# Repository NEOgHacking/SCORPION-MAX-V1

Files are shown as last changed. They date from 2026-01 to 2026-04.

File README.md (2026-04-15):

# 3D printer / CNC Mainboard
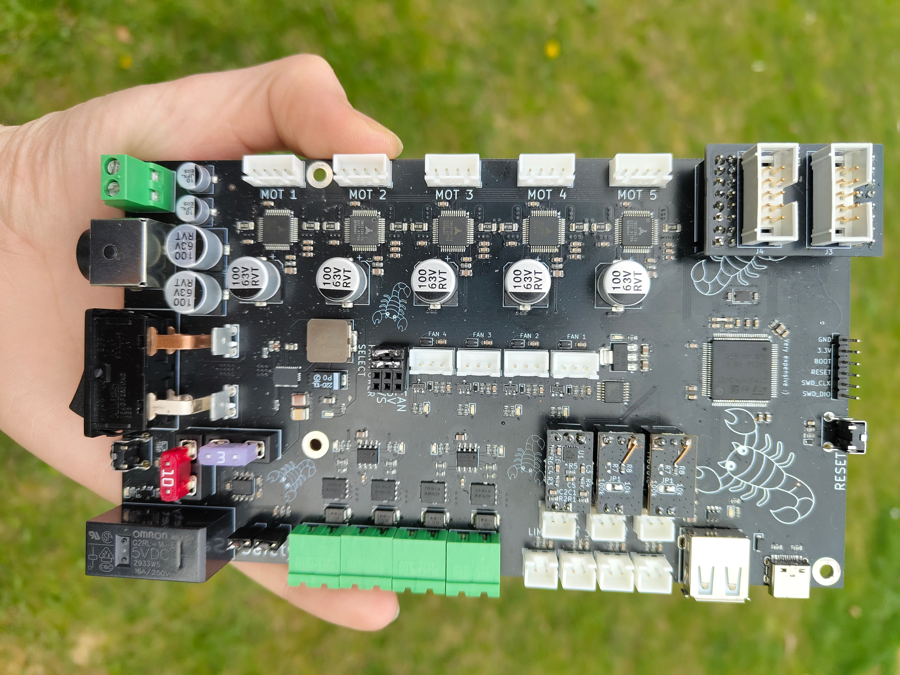
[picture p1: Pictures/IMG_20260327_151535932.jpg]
PCB SCORPION MAX V1

PCB SCORPION MAX V1
A main board for a 3d printer or CNC with wide possibilities with the use of the expansion board and thermistor boards! This board is based on the STM32H743 for its massive power. And everyone hates loud stepper motors, so it uses the TMC2130 silent stepper drivers, these are not only very quiet but have a lot of other functions!

# Video of working
Watch the video (https://youtube.com/shorts/JvQLqBAzKsY?feature=share)
# Reason
So long story longer I have an ultimaker 2+ laying at home doing nothing because of the noisy stepper drivers and recently getting an ultimaker S5 so I wanted to make it quieter and more useful. I was amazed by the Prusa mini being so quiet, so I thought why not build my own mainboard with way more quiet stepper drivers and more functions. The second reason is that I am planning to build a CNC somewhere in the future so I thought it would be a genius idea to build my own 3D printer / CNC mainboard with my own overkill specs and the best stepper drivers. And most of all A LOT of power in amps and compute!

# Specs
5x Stepper driver TMC2130

4x Power Mosfets for controlling heated beds, heaters, ext.

4x Fan controller with tacho input

4x Limit switches for homing

3x Thermistor inputs with possibilities for NTC's and PTC's
  These possibilities are possible because of the 2 thermistor boards I have designed, and the NTC thermistor board has a solder jumper to select the resistance of you NTC.

2x Safety inputs for disabling cutting power via a relay to the stepper drivers and mosfets

Expansion port for displays, SD cards, ext.

STM32H743VIT6 for big storage and calculation power

Standard 4 pin power connector and 2 pin screw terminal

USB ports, USB-C for programming and external control and USB-A for USB flash drives

# Design
This board is designed with a lot of safety features and well thought out design, it has a safety circuit to cut power to the steppers and heaters, good pcb design, followed design recommendation from datasheets, used the right components, and allot more! The pcb has been designed with the right trace width and good trace layout with no sharp bends. Also have good pcb layout.
# Schematics
There are 3 schematics for this project:
1. Main board
2. Thermistor modules
3. Expansion module

These are way too long to display here (14 pages) so in the PCB folder there in folder for the board you want to see there is a pdf file of the schematic, but here are a few.
Printer Mainboard page 1
Printer Mainboard page 9
Printer Mainboard page 10
Expansion board
PTC
NTC

# PCB

Main board




Thermistor boards




Expansion board




# Panalization
I have panelized the thermistor boards for better price per board, the panel still is under the 100x100 limit for the 2 dollar offer on jlcpcb so it’s still very cheap. I needed 6 thermistors for 2 boards and minimum order quantity on jlcpcb is 5, so I made a panel.



# Firmware
The firmware provided is Marlin, but I plan to expand this to more firmware’s like Clipper ext. The board is based on the STM32H743 so it's very powerful and can run almost any firmware!

# BOM
I have made a BOM for LCSC and a global BOM for all the parts and PCBs these are in the BOM folder
The price of the LCSC BOM for all the parts is about 180 dollars for 2 boards and the JLCPCB order is at the 54 dollar.
This is not the cheapest board but it does have the most functions!

# Credits
@Kai Pereira for all my random questions regarding PCB design and blueprint custom project. and for telling me long journals are the best, sorry for the short ones at the beginning. whoops.
Henk, someone I know that is way better in PCB design than me that looked over my schematic and layout ext.

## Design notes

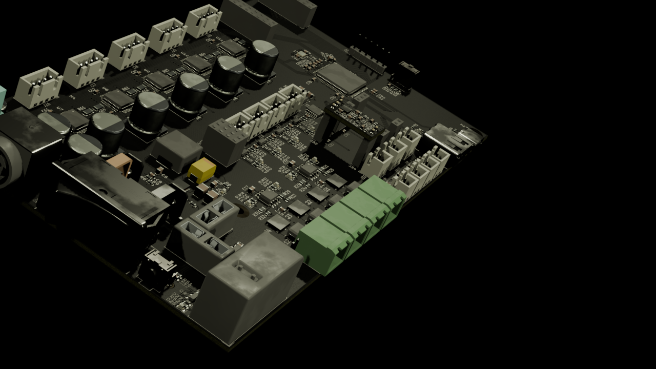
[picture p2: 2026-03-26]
Pictures/Renders/Render SCORPION MAX V1.png0072.png

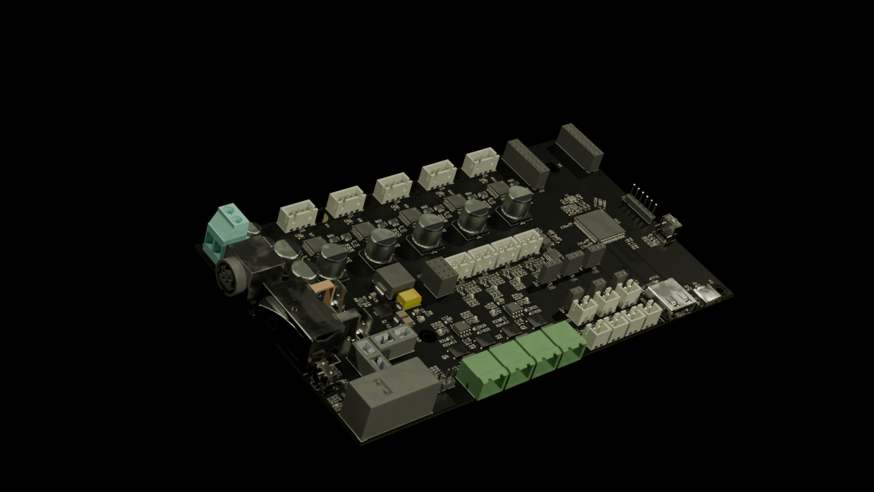
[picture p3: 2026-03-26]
Pictures/Renders/Render SCORPION MAX V1.png0001.png

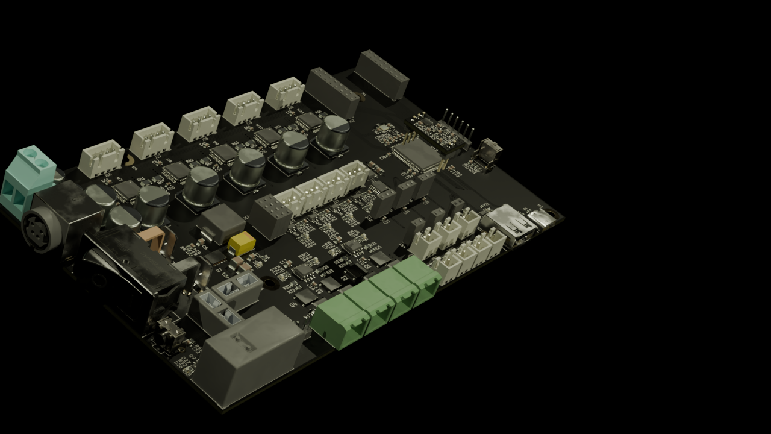
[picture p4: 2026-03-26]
Pictures/Renders/Render SCORPION MAX V1.png0026.png

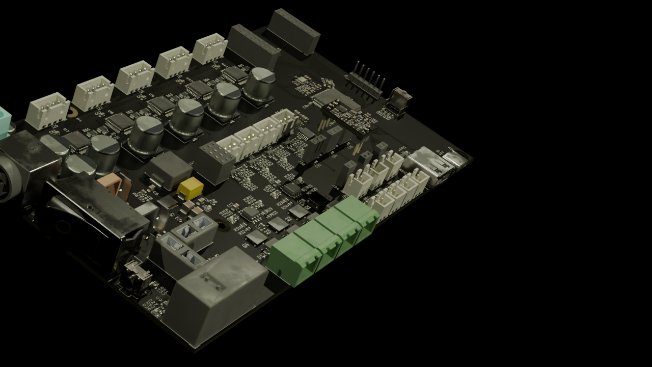
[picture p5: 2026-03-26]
Pictures/Renders/Render SCORPION MAX V1.png0035.png

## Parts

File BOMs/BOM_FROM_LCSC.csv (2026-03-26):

SCORPION MAX V1 |  |  |  |  |  |  |  |  |  | LCSC BOM Quotation
 |  |  |  |  |  |  |  |  |  | BOM Date Created：11/01/26 03:50:32 |  |  |  | BOM Export Date: 12/01/26 06:11:32 |  |  |  | The matching result is a real-time query result, availability and prices may fluctuate. Backorder items are estimated prices for your reference, please submit "Create Quote" to get the real price. All information is provided "as is" and is subject to change without notice. Any use made of the information provided is without recourse to LCSC and at the user's risk.
 |  |  |  |  |  |  |  |  |  | EST TOTAL :$156.41 |  |  |  | Website：https://www.lcsc.com/bom
Uploaded data |  |  |  |  |  |  |  |  |  | LCSC Matching Results
LCSC# | Mfr. | Mrf# | Description | Package | Value | Customer Part Number | Quantity | Target Price(EUR) | Target Lead Time(Business Days) | Mrf# | Mfr. | Order Qty. | Unit Price(EUR) | Ext.Price(EUR) | LCSC# | Package | Min | Mult | SPQ | Availability | Stock Status | Customer Notes | Description | Matched status | Product Link
 |  |  |  |  |  | 28 | 5 |  |  | TYPE-C-31-M-12 | Korean Hroparts Elec | 5 | 0.1553 | 0.78 | C165948 | SMD | 5 | 5 | 1000 | 428540 | In Stock |  | USB-C (USB TYPE-C) Receptacle Connector 16 Position Surface Mount | Exact Matches | https://www.lcsc.com/product-detail/C165948.html
 |  |  |  |  |  | 19 | 10 |  |  | SMBJ64A | R+O | 10 | 0.0441 | 0.44 | C19077594 | DO-214AA(SMB) | 10 | 10 | 3000 | 70550 | In Stock |  | 103VC Clamp 5.83A@10/1000us Ipp TVS DIODE DO-214AA(SMB) | Exact Matches | https://www.lcsc.com/product-detail/C19077594.html
 |  |  |  |  |  | 22 | 50 |  |  | 1N5819WS | Guangdong Hottech | 50 | 0.0083 | 0.42 | C191023 | SOD-323 | 50 | 50 | 3000 | 2274200 | In Stock |  | Diode 40V 1A Surface Mount SOD-323 | Exact Matches | https://www.lcsc.com/product-detail/C191023.html
 |  |  |  |  |  | 23 | 100 |  |  | 1N4148WT | JSMSEMI | 100 | 0.0050 | 0.50 | C917006 | SOD-523 | 100 | 100 | 3000 | 942700 | In Stock |  | Diode Independent 75V 150mA Surface Mount SOD-523 | Exact Matches | https://www.lcsc.com/product-detail/C917006.html
 |  |  |  |  |  | 24 | 10 |  |  | BAT54KFILM | ST | 10 | 0.0684 | 0.68 | C283259 | SOD-523 | 10 | 10 | 3000 | 2120 | In Stock |  | Diode 40V 300mA Surface Mount SOD-523 | Exact Matches | https://www.lcsc.com/product-detail/C283259.html
 |  |  |  |  |  | 43 | 2 |  |  | IHLP4040DZER6R8M01 | VISHAY | 2 | 0.8322 | 1.66 | C845080 | SMD,10.8x10.2mm | 1 | 1 | 500 | 48 | In Stock |  | 8A 6.8uH ±20% 23.3mΩ 13.5A SMD,10.8x10.2mm Fixed Inductors RoHS | Exact Matches | https://www.lcsc.com/product-detail/C845080.html
 |  |  |  |  |  | 27 | 2 |  |  | USB-302-T | SOFNG | 2 | 0.1055 | 0.21 | C112456 | Through Hole,Right Angle | 1 | 1 | 100 | 7704 | In Stock |  | USB-A (USB TYPE-A) Receptacle Connector 4 Position Right Angle | Exact Matches | https://www.lcsc.com/product-detail/C112456.html
 |  |  |  |  |  | 71 | 5 |  |  | NE555DR | TI | 5 | 0.0852 | 0.43 | C7593 | SOIC-8 | 5 | 5 | 2500 | 115150 | In Stock |  | SOIC-8 Programmable Timers and Oscillators RoHS | Exact Matches | https://www.lcsc.com/product-detail/C7593.html
 |  |  |  |  |  | 64 | 5 |  |  | STMPS2141STR | ST | 5 | 0.2987 | 1.49 | C54624 | SOT-23-5 | 5 | 5 | 3000 | 2220 | In Stock |  | SOT-23-5 Power Distribution Switches, Load Drivers RoHS | Exact Matches | https://www.lcsc.com/product-detail/C54624.html
 |  |  |  |  |  | 72 | 10 |  |  | TMC2130-TA-T | TRINAMIC | 10 | 4.3494 | 43.49 | C328952 | TQFP-48-EP(7x7) | 1 | 1 | 2000 | 1640 | In Stock |  | TQFP-48-EP(7x7) Motor Drivers, Controllers RoHS | Exact Matches | https://www.lcsc.com/product-detail/C328952.html
 |  |  |  |  |  | 68 | 5 |  |  | AP7361C-33E-13 | DIODES | 5 | 0.2142 | 1.07 | C500795 | SOT-223 | 5 | 5 | 2500 | 250 | In Stock |  | 6V Positive Fixed 3.3V SOT-223 Voltage Regulators - Linear, Low Drop Out (LDO) Regulators RoHS | Exact Matches | https://www.lcsc.com/product-detail/C500795.html
 |  |  |  |  |  | 67 | 5 |  |  | USBLC6-2SC6 | ST | 5 | 0.1155 | 0.58 | C7519 | SOT-23-6L | 5 | 5 | 3000 | 9985 | In Stock |  | 17VC Clamp 5A Ipp ESD DIODE SOT-23-6L | Exact Matches | https://www.lcsc.com/product-detail/C7519.html
 |  |  |  |  |  | 74 | 5 |  |  | NX3225GA-25.000M-STD-CRG-2 | NDK | 5 | 0.2464 | 1.23 | C1985619 | SMD3225-4P | 5 | 5 | 3000 | 1600 | In Stock |  | Crystal 25MHz ±20ppm 8pF 50Ω SMD3225-4P | Exact Matches | https://www.lcsc.com/product-detail/C1985619.html
 |  |  |  |  |  | 44 | 10 |  |  | NVMFWS4D5N08XT1G | onsemi | 10 | 1.5580 | 15.58 | C29841638 | DFNW-5(5x6) | 1 | 1 | 1500 | 48 | In Stock |  | 80V 92A 3.6V 4.5mΩ@10V 1 N-channel 82W DFNW-5(5x6) Single FETs, MOSFETs RoHS | Exact Matches | https://www.lcsc.com/product-detail/C29841638.html
 |  |  |  |  |  | 66 | 5 |  |  | B3F-3120 | OMRON | 5 | 0.1885 | 0.94 | C231318 | Through Hole | 5 | 5 | 1000 | 2070 | In Stock |  | Tactile Switch SPST 100gf 1.6mm PC Pin Through Hole, Right Angle | Exact Matches | https://www.lcsc.com/product-detail/C231318.html
 |  |  |  |  |  | 34 | 10 |  |  | 63849-1 | TE Connectivity | 10 | 0.0578 | 0.58 | C86469 | Through Hole | 10 | 10 | 2000 | 11260 | In Stock |  | Through Hole Quick Connects, Quick Disconnect Connectors RoHS | Exact Matches | https://www.lcsc.com/product-detail/C86469.html
 |  |  |  |  |  | 36 | 2 |  |  | 1711725 | Phoenix Contact | 2 | 0.9011 | 1.80 | C89120 | Through Hole,P=5.08mm | 1 | 1 | 100 | 893 | In Stock |  | 2 Position Wire to Board Terminal Block Through Hole 5.08mm | Exact Matches | https://www.lcsc.com/product-detail/C89120.html
 |  |  |  |  |  | 302 | 5 |  |  | SS11-BBIWG-R20-R | Legion | 5 | 0.2283 | 1.14 | C309069 | Through Hole,21x15mm | 5 | 5 | 500 | 2870 | In Stock |  | Rocker Switch SPST 16A(AC) 250V Through Hole | Exact Matches | https://www.lcsc.com/product-detail/C309069.html
 |  |  |  |  |  | 25 | 5 |  |  | XF-508P-B-B | XFCN | 5 | 0.2015 | 1.01 | C19727305 | DIP-4 | 5 | 5 | 500 | 28605 | In Stock |  | Blade 15A Clip 1 DIP-4 Fuseholders RoHS | Exact Matches | https://www.lcsc.com/product-detail/C19727305.html
 |  |  |  |  |  | 301 | 10 |  |  | 1757019 | Phoenix Contact | 10 | 0.6432 | 6.43 | C90073 | P=5.08mm | 1 | 1 | 100 | 1840 | In Stock |  | 2 Position Plug 5.08mm Pitch | Exact Matches | https://www.lcsc.com/product-detail/C90073.html
 |  |  |  |  |  | 65 | 2 |  |  | SDDJF31100 | ALPSALPINE | 2 | 2.7511 | 5.50 | C380204 | Through Hole | 1 | 1 | 100 | 251 | In Stock |  | Rocker Switch DPST 16A(AC) 250V Through Hole | Exact Matches | https://www.lcsc.com/product-detail/C380204.html
 |  |  |  |  |  | 17 | 10 |  |  | DSK24L | LGE | 10 | 0.0500 | 0.50 | C19272974 | SOD-123FL | 10 | 10 | 3000 | 70 | In Stock |  | Diode Independent 40V 2A Surface Mount SOD-123FL | Exact Matches | https://www.lcsc.com/product-detail/C19272974.html
 |  |  |  |  |  | 45 | 20 |  |  | BC817-40,215 | Nexperia | 20 | 0.0306 | 0.61 | C52801 | SOT-23 | 20 | 20 | 3000 | 0 | Backordered |  | Bipolar (BJT) Transistor NPN 45V 500mA 100MHz 345mW Surface Mount SOT-23 | Exact Matches | https://www.lcsc.com/product-detail/C52801.html
 |  |  |  |  |  | 46 | 20 |  |  | BC807-40,215 | Nexperia | 20 | 0.0280 | 0.56 | C57316 | SOT-23 | 20 | 20 | 3000 | 145000 | In Stock |  | Bipolar (BJT) Transistor PNP 45V 500mA 80MHz 250mW Surface Mount SOT-23 | Exact Matches | https://www.lcsc.com/product-detail/C57316.html
 |  |  |  |  |  | 26 | 2 |  |  | LM76005QRNPRQ1 | TI | 2 | 4.7957 | 9.59 | C2873394 | WQFN-30(4x6) | 1 | 1 | 3000 | 76 | In Stock |  | Buck Switching Regulator IC Adjustable 1V~57V 1 Output 5A WQFN-30(4x6) | Exact Matches | https://www.lcsc.com/product-detail/C2873394.html
 |  |  |  |  |  | 29 | 20 |  |  | B2B-XH-A(LF)(SN) | JST | 20 | 0.0308 | 0.62 | C158012 | Through Hole,P=2.5mm | 20 | 20 | 1000 | 292080 | In Stock |  | Connector Header 2 position 2.5mm Pitch 3A Through Hole -25℃~+85℃ | Exact Matches | https://www.lcsc.com/product-detail/C158012.html
 |  |  |  |  |  | 39 | 20 |  |  | PZ2.54-1X6P-H25 | JXTCONN | 20 | 0.0099 | 0.20 | C42431790 | Through Hole,P=2.54mm | 20 | 20 | 2000 | 5320 | In Stock |  | Pin Header 6 Position 2.54mm Pitch Single Row Through Hole -40℃~+105℃ | Exact Matches | https://www.lcsc.com/product-detail/C42431790.html
 |  |  |  |  |  | 40 | 10 |  |  | PM2.54-1X3P-H85 | JXTCONN | 10 | 0.0262 | 0.26 | C42431866 | Through Hole,P=2.54mm | 5 | 5 | 500 | 8210 | In Stock |  | 3A 3P Through Hole -40℃~+105℃ 8.5mm Gold 1x3P 2.54mm Top 1 Square Hole Through Hole,P=2.54mm Headers, Receptacles, Female Sockets RoHS | Exact Matches | https://www.lcsc.com/product-detail/C42431866.html
 |  |  |  |  |  | 31 | 10 |  |  | PM2.54-2X8PM-H85 | JXTCONN | 10 | 0.0577 | 0.58 | C42431844 | Through Hole,P=2.54mm | 5 | 5 | 200 | 1395 | In Stock |  | Female Header 16 Position 2.54mm Pitch Dual Row Through Hole -40℃~+105℃ | Exact Matches | https://www.lcsc.com/product-detail/C42431844.html
 |  |  |  |  |  | 32 | 10 |  |  | PM2.54-1X4PM-H85 | JXTCONN | 10 | 0.0553 | 0.55 | C42431839 | Through Hole,P=2.54mm | 5 | 5 | 500 | 2015 | In Stock |  | Female Header 4 Position 2.54mm Pitch Single Row Through Hole -40℃~+105℃ | Exact Matches | https://www.lcsc.com/product-detail/C42431839.html
 |  |  |  |  |  | 41 | 10 |  |  | PM2.54-1X2PM-H85 | JXTCONN | 10 | 0.0544 | 0.54 | C42431841 | Through Hole,P=2.54mm | 5 | 5 | 1000 | 8450 | In Stock |  | Female Header 2 Position 2.54mm Pitch Single Row Through Hole -40℃~+105℃ | Exact Matches | https://www.lcsc.com/product-detail/C42431841.html
 |  |  |  |  |  | 33 | 10 |  |  | B3B-XH-A(LF)(SN) | JST | 10 | 0.0414 | 0.41 | C144394 | Through Hole,P=2.5mm | 10 | 10 | 1000 | 176710 | In Stock |  | Connector Header 3 position 2.5mm Pitch 3A Through Hole -25℃~+85℃ | Exact Matches | https://www.lcsc.com/product-detail/C144394.html
 |  |  |  |  |  | 38 | 20 |  |  | B4B-XH-A(LF)(SN) | JST | 20 | 0.0449 | 0.90 | C144395 | Through Hole,P=2.5mm | 10 | 10 | 500 | 182050 | In Stock |  | Connector Header 4 position 2.5mm Pitch 3A Through Hole -25℃~+85℃ | Exact Matches | https://www.lcsc.com/product-detail/C144395.html
 |  |  |  |  |  | 63 | 40 |  |  | FBF06FTPR120-00L | PSA | 40 | 0.0205 | 0.82 | C382272 | 1206 | 20 | 20 | 5000 | 320 | In Stock |  | 120mΩ ±1% 750mW | Exact Matches | https://www.lcsc.com/product-detail/C382272.html
 |  |  |  |  |  | 4 | 2 |  |  | 593D227X0010E2TE3 | VISHAY | 2 | 0.4228 | 0.85 | C1952898 | CASE-E-7343-43(mm) | 1 | 1 | 400 | 41 | In Stock |  | 220uF ±20% 10V Tantalum Capacitors 100mΩ 2917 | Exact Matches | https://www.lcsc.com/product-detail/C1952898.html
 |  |  |  |  |  | 3 | 5 |  |  | VJ0805Y474KXQTW1BC | VISHAY | 5 | 0.0519 | 0.26 | C2177586 | 0805 | 5 | 5 | 3000 | 35 | In Stock |  | 470nF ±10% 10V Ceramic Capacitor X7R 0805 | Exact Matches | https://www.lcsc.com/product-detail/C2177586.html
 |  |  |  |  |  | 5 | 3 |  |  | VJ1210Y474KXBAT | VISHAY | 3 | 0.4224 | 1.27 | C2313088 | 1210 | 1 | 1 | 2000 | 24 | In Stock |  | 470nF ±10% 100V Ceramic Capacitor X7R 1210 | Exact Matches | https://www.lcsc.com/product-detail/C2313088.html
 |  |  |  |  |  | 6 | 5 |  |  | C3225X7S2A475KT003S | TDK | 5 | 0.4065 | 2.03 | C694475 | 1210 | 1 | 1 | 1000 | 525 | In Stock |  | 100V 4.7uF X7S ±10% 1210 Ceramic Capacitors RoHS | Exact Matches | https://www.lcsc.com/product-detail/C694475.html
 |  |  |  |  |  | 7 | 5 |  |  | C1608X5R1C225KT000N | TDK | 5 | 0.0310 | 0.16 | C76612 | 0603 | 5 | 5 | 4000 | 2490 | In Stock |  | 2.2uF ±10% 16V Ceramic Capacitor X5R 0603 | Exact Matches | https://www.lcsc.com/product-detail/C76612.html
 |  |  |  |  |  | 9 | 5 |  |  | EEEFK1J100P | PANASONIC | 5 | 0.1279 | 0.64 | C128459 | SMD,D6.3xL5.8mm | 5 | 5 | 1000 | 6980 | In Stock |  | 10uF ±20% 63V Aluminum Electrolytic Capacitors 2000hrs@105℃ | Exact Matches | https://www.lcsc.com/product-detail/C128459.html
 |  |  |  |  |  | 10 | 100 |  |  | CC0603KRX7R9BB103 | YAGEO | 100 | 0.0020 | 0.20 | C100042 | 0603 | 100 | 100 | 4000 | 7339600 | In Stock |  | 10nF ±10% 50V Ceramic Capacitor X7R 0603 | Exact Matches | https://www.lcsc.com/product-detail/C100042.html
 |  |  |  |  |  | 1 | 200 |  |  | CC0603KRX7R9BB104 | YAGEO | 200 | 0.0019 | 0.38 | C14663 | 0603 | 100 | 100 | 4000 | 23529600 | In Stock |  | 100nF ±10% 50V Ceramic Capacitor X7R 0603 | Exact Matches | https://www.lcsc.com/product-detail/C14663.html
 |  |  |  |  |  | 13 | 50 |  |  | CL10A105KB8NNNC | Samsung Electro-Mechanics | 50 | 0.0046 | 0.23 | C15849 | 0603 | 50 | 50 | 4000 | 8315200 | In Stock |  | 1uF ±10% 50V Ceramic Capacitor X5R 0603 | Exact Matches | https://www.lcsc.com/product-detail/C15849.html
 |  |  |  |  |  | 12 | 100 |  |  | CC0603KRX7R9BB223 | YAGEO | 100 | 0.0027 | 0.27 | C106222 | 0603 | 100 | 100 | 4000 | 1160800 | In Stock |  | 22nF ±10% 50V Ceramic Capacitor X7R 0603 | Exact Matches | https://www.lcsc.com/product-detail/C106222.html
 |  |  |  |  |  | 14 | 50 |  |  | CL10C080DB81PNC | Samsung Electro-Mechanics | 50 | 0.0087 | 0.44 | C346204 | 0603 | 50 | 50 | 4000 | 10650 | In Stock |  | 8pF 50V Ceramic Capacitor C0G 0603 | Exact Matches | https://www.lcsc.com/product-detail/C346204.html
 |  |  |  |  |  | 2 | 50 |  |  | CL21A475KBQNNNE | Samsung Electro-Mechanics | 50 | 0.0172 | 0.86 | C98192 | 0805 | 10 | 10 | 2000 | 3008340 | In Stock |  | 4.7uF ±10% 50V Ceramic Capacitor X5R 0805 | Exact Matches | https://www.lcsc.com/product-detail/C98192.html
 |  |  |  |  |  | 37 | 50 |  |  | PH2.54-1X2P-H25 | JXTCONN | 50 | 0.0052 | 0.26 | C42431798 | Through Hole,P=2.54mm | 50 | 50 | 2000 | 57250 | In Stock |  | Pin Header 2 Position 2.54mm Pitch Single Row Through Hole -40℃~+105℃ | Exact Matches | https://www.lcsc.com/product-detail/C42431798.html
 |  |  |  |  |  | 11 | 50 |  |  | CC0603KRX7R9BB474 | YAGEO | 50 | 0.0076 | 0.38 | C513577 | 0603 | 50 | 50 | 4000 | 693950 | In Stock |  | 470nF ±10% 50V Ceramic Capacitor X7R 0603 | Exact Matches | https://www.lcsc.com/product-detail/C513577.html
 |  |  |  |  |  | 15 | 50 |  |  | CL10A225KB8NNNC | Samsung Electro-Mechanics | 50 | 0.0187 | 0.94 | C913904 | 0603 | 10 | 10 | 4000 | 322070 | In Stock |  | 2.2uF ±10% 50V Ceramic Capacitor X5R 0603 | Exact Matches | https://www.lcsc.com/product-detail/C913904.html
 |  |  |  |  |  | 35 | 5 |  |  | DIN-422 | HOOYA | 5 | 0.2494 | 1.25 | C2939341 | Through Hole | 5 | 5 | 100 | 0 | Backordered |  | 6.5A -25℃~+85℃ Through Hole Circular Connector Assemblies RoHS | Exact Matches | https://www.lcsc.com/product-detail/C2939341.html
 |  |  |  |  |  | 57 | 100 |  |  | RC0603FR-07100RL | YAGEO | 100 | 0.0012 | 0.12 | C105588 | 0603 | 100 | 100 | 5000 | 1118300 | In Stock |  | 100mW 100Ω 75V Thick Film Resistor ±100ppm/℃ ±1% 0603 Chip Resistor - Surface Mount RoHS | Exact Matches | https://www.lcsc.com/product-detail/C105588.html
 |  |  |  |  |  | 50 | 100 |  |  | RC0603FR-07120RL | YAGEO | 100 | 0.0013 | 0.13 | C114640 | 0603 | 100 | 100 | 5000 | 76300 | In Stock |  | 100mW 120Ω 75V Thick Film Resistor ±100ppm/℃ ±1% 0603 Chip Resistor - Surface Mount RoHS | Exact Matches | https://www.lcsc.com/product-detail/C114640.html
 |  |  |  |  |  | 62 | 100 |  |  | RC0603FR-0710RL | YAGEO | 100 | 0.0028 | 0.28 | C109318 | 0603 | 100 | 100 | 5000 | 687500 | In Stock |  | 100mW 10Ω 75V Thick Film Resistor ±1% ±200ppm/℃ 0603 Chip Resistor - Surface Mount RoHS | Exact Matches | https://www.lcsc.com/product-detail/C109318.html
 |  |  |  |  |  | 58 | 100 |  |  | RC0805FR-0710RL | YAGEO | 100 | 0.0047 | 0.47 | C96347 | 0805 | 100 | 100 | 5000 | 101000 | In Stock |  | 10Ω 125mW 150V Thick Film Resistor ±1% ±200ppm/℃ 0805 Chip Resistor - Surface Mount RoHS | Exact Matches | https://www.lcsc.com/product-detail/C96347.html
 |  |  |  |  |  | 51 | 100 |  |  | RC0603FR-07470RL | YAGEO | 100 | 0.0013 | 0.13 | C114669 | 0603 | 100 | 100 | 5000 | 235200 | In Stock |  | 100mW 470Ω 75V Thick Film Resistor ±100ppm/℃ ±1% 0603 Chip Resistor - Surface Mount RoHS | Exact Matches | https://www.lcsc.com/product-detail/C114669.html
 |  |  |  |  |  | 48 | 100 |  |  | RC0603FR-07620RL | YAGEO | 100 | 0.0012 | 0.12 | C137695 | 0603 | 100 | 100 | 5000 | 145200 | In Stock |  | 620Ω 100mW 75V Thick Film Resistor ±100ppm/℃ ±1% 0603 Chip Resistor - Surface Mount RoHS | Exact Matches | https://www.lcsc.com/product-detail/C137695.html
 |  |  |  |  |  | 55 | 100 |  |  | RC0603FR-071KL | YAGEO | 100 | 0.0012 | 0.12 | C22548 | 0603 | 100 | 100 | 5000 | 2322600 | In Stock |  | 100mW 1kΩ 75V Thick Film Resistor ±100ppm/℃ ±1% 0603 Chip Resistor - Surface Mount RoHS | Exact Matches | https://www.lcsc.com/product-detail/C22548.html
 |  |  |  |  |  | 60 | 100 |  |  | RC0603FR-071K8L | YAGEO | 100 | 0.0012 | 0.12 | C185354 | 0603 | 100 | 100 | 5000 | 177300 | In Stock |  | 100mW 1.8kΩ 75V Thick Film Resistor ±100ppm/℃ ±1% 0603 Chip Resistor - Surface Mount RoHS | Exact Matches | https://www.lcsc.com/product-detail/C185354.html
 |  |  |  |  |  | 61 | 100 |  |  | RC0603FR-0710KL | YAGEO | 100 | 0.0012 | 0.12 | C98220 | 0603 | 100 | 100 | 5000 | 3570900 | In Stock |  | 100mW 10kΩ 75V Thick Film Resistor ±100ppm/℃ ±1% 0603 Chip Resistor - Surface Mount RoHS | Exact Matches | https://www.lcsc.com/product-detail/C98220.html
 |  |  |  |  |  | 54 | 100 |  |  | RC0603FR-074K7L | YAGEO | 100 | 0.0012 | 0.12 | C99782 | 0603 | 100 | 100 | 5000 | 1705600 | In Stock |  | 100mW 4.7kΩ 75V Thick Film Resistor ±100ppm/℃ ±1% 0603 Chip Resistor - Surface Mount RoHS | Exact Matches | https://www.lcsc.com/product-detail/C99782.html
 |  |  |  |  |  | 52 | 20 |  |  | -(The data has been deleted.) | - | - | - | - | - | - | - | - | - | - | - | - | - | -
 |  |  |  |  |  | 53 | 50 |  |  | RT0603BRE0724K9L | YAGEO | 50 | 0.0184 | 0.92 | C861775 | 0603 | 50 | 50 | 5000 | 250 | In Stock |  | 24.9kΩ 100mW 75V Thin Film Resistor ±50ppm/℃ ±0.1% 0603 Chip Resistor - Surface Mount RoHS | Exact Matches | https://www.lcsc.com/product-detail/C861775.html
 |  |  |  |  |  | 49 | 100 |  |  | RC0603FR-075K1L | YAGEO | 100 | 0.0013 | 0.13 | C105580 | 0603 | 100 | 100 | 5000 | 225400 | In Stock |  | 100mW 5.1kΩ 75V Thick Film Resistor ±100ppm/℃ ±1% 0603 Chip Resistor - Surface Mount RoHS | Exact Matches | https://www.lcsc.com/product-detail/C105580.html
 |  |  |  |  |  | 18 | 20 |  |  | A-SP192DGHC-C01-4T | Amicc | 20 | 0.0199 | 0.40 | C19171301 | 0603 | 20 | 20 | 4000 | 363940 | In Stock |  | Green 518nm LED Indication - Discrete 2.4V~3V 0603 | Exact Matches | https://www.lcsc.com/product-detail/C19171301.html
 |  |  |  |  |  | 20 | 20 |  |  | A-SP192DB1C-C01-4T | Amicc | 20 | 0.0283 | 0.57 | C5355419 | 0603 | 20 | 20 | 4000 | 3180 | In Stock |  | Blue 470nm LED Indication - Discrete 2.6V~3.2V 0603 | Exact Matches | https://www.lcsc.com/product-detail/C5355419.html
 |  |  |  |  |  | 21 | 20 |  |  | A-SP192DG2C-C01-4T | Amicc | 20 | 0.0236 | 0.47 | C5151486 | 0603 | 20 | 20 | 4000 | 760 | In Stock |  | Yellow Green 575nm LED Indication - Discrete 2.3V 0603 | Exact Matches | https://www.lcsc.com/product-detail/C5151486.html
 |  |  |  |  |  | 16 | 20 |  |  | A-SP192XR5C-A01-4T | Amicc | 20 | 0.0189 | 0.38 | C19171307 | 0603 | 20 | 20 | 4000 | 3740 | In Stock |  | Red 639nm LED Indication - Discrete 1.7V~2.2V 0603 | Exact Matches | https://www.lcsc.com/product-detail/C19171307.html
 |  |  |  |  |  | 8 | 20 |  |  | RVT1J101M1010 | ROQANG | 20 | 0.0804 | 1.61 | C72481 | SMD,D10xL10.2mm | 5 | 5 | 500 | 51190 | In Stock |  | 100uF ±20% 63V Aluminum Electrolytic Capacitors 2000hrs@105℃ | Exact Matches | https://www.lcsc.com/product-detail/C72481.html
 |  |  |  |  |  | 56 | 100 |  |  | RC0603FR-07430RL | YAGEO | 100 | 0.0012 | 0.12 | C137721 | 0603 | 100 | 100 | 5000 | 158400 | In Stock |  | 100mW 430Ω 75V Thick Film Resistor ±100ppm/℃ ±1% 0603 Chip Resistor - Surface Mount RoHS | Exact Matches | https://www.lcsc.com/product-detail/C137721.html
 |  |  |  |  |  | 42 | 2 |  |  | G2RL-1A-E DC5 | OMRON | 2 | 2.7345 | 5.47 | C397259 | DIP | 1 | 1 | 20 | 15 | In Stock |  | 16A 5V 1 Set Normally Open: 1A (SPST NO) DIP Power Relays RoHS | Exact Matches | https://www.lcsc.com/product-detail/C397259.html
 |  |  |  |  |  | 59 | 100 |  |  | RC0603FR-07536RL | YAGEO | 100 | 0.0013 | 0.13 | C245976 | 0603 | 100 | 100 | 5000 | 4600 | In Stock |  | 100mW 536Ω 75V Thick Film Resistor ±100ppm/℃ ±1% 0603 Chip Resistor - Surface Mount RoHS | Exact Matches | https://www.lcsc.com/product-detail/C245976.html
 |  |  |  |  |  | 110 | 4 |  |  | INA826AIDRGR | TI | 4 | 2.0966 | 8.39 | C2870890 | WSON-8-EP(3x3) | 1 | 1 | 3000 | 96 | In Stock |  | WSON-8-EP(3x3) Amplifiers RoHS | Exact Matches | https://www.lcsc.com/product-detail/C2870890.html
 |  |  |  |  |  | 73 | 2 |  |  | STM32H743VIT6 | ST | 2 | 6.1268 | 12.25 | C114409 | LQFP-100(14x14) | 1 | 1 | 90 | 4000 | In Stock |  | ARM Cortex-M7 32 Bit 480MHz 82 LQFP-100(14x14) Microcontrollers RoHS | Exact Matches | https://www.lcsc.com/product-detail/C114409.html
 |  |  |  |  |  | 30 | 1 |  |  | 1923869 | Phoenix Contact | 1 | 0.5341 | 0.53 | C5443585 | P=5.08mm | 1 | 1 | 50 | 2 | In Stock |  | 2P 5.08mm Green 2 1 Straight Pin P=5.08mm Headers, Plugs and Sockets RoHS | Exact Matches | https://www.lcsc.com/product-detail/C5443585.html
 |  |  |  |  |  | 69 | 5 |  |  | TC4427EOA | MICROCHIP | 5 | 1.1397 | 5.70 | C636891 | SOIC-8 | 1 | 1 | 100 | 1168 | In Stock |  | 1.5A 4.5V~18V SOIC-8 Gate Drivers RoHS | Exact Matches | https://www.lcsc.com/product-detail/C636891.html
 |  |  |  |  |  | 70 | 3 |  |  | SN74LV4T125PWR | TI | 3 | 0.5946 | 1.78 | C90755 | TSSOP-14 | 1 | 1 | 2000 | 2208 | In Stock |  | 1.6V~5.5V 1 4 3.2ns@5V,15pF 20uA TSSOP-14 Buffers, Drivers, Receivers, Transceivers RoHS | Exact Matches | https://www.lcsc.com/product-detail/C90755.html
 |  |  |  |  |  | 47 | 100 |  |  | RC0603FR-0747KL | YAGEO | 100 | 0.0012 | 0.12 | C105579 | 0603 | 100 | 100 | 5000 | 273000 | In Stock |  | 100mW 47kΩ 75V Thick Film Resistor ±100ppm/℃ ±1% 0603 Chip Resistor - Surface Mount RoHS | Exact Matches | https://www.lcsc.com/product-detail/C105579.html
 |  |  |  |  |  | 52 | 20 |  |  | RT0603BRE07100KL | YAGEO | 20 | 0.0167 | 0.33 | C326758 | 0603 | 20 | 20 | 5000 | 67860 | In Stock |  | 100kΩ 100mW 75V Thin Film Resistor ±50ppm/℃ ±0.1% 0603 Chip Resistor - Surface Mount RoHS | Exact Matches | https://www.lcsc.com/product-detail/C326758.html
 |  |  |  |  |  | 105 | 100 |  |  | RC0603FR-072K2L | YAGEO | 100 | 0.0012 | 0.12 | C114662 | 0603 | 100 | 100 | 5000 | 150000 | In Stock |  | 100mW 2.2kΩ 75V Thick Film Resistor ±100ppm/℃ ±1% 0603 Chip Resistor - Surface Mount RoHS | Exact Matches | https://www.lcsc.com/product-detail/C114662.html
 |  |  |  |  |  | 103 | 50 |  |  | PH2.54-1X3P-H25 | JXTCONN | 50 | 0.0052 | 0.26 | C42431836 | Through Hole,P=2.54mm | 50 | 50 | 2000 | 40900 | In Stock |  | Pin Header 3 Position 2.54mm Pitch Single Row Through Hole -40℃~+105℃ | Exact Matches | https://www.lcsc.com/product-detail/C42431836.html
 |  |  |  |  |  | 304 | 5 |  |  | 0297003.WXNV | Littelfuse | 5 | 0.1098 | 0.55 | C151092 | - | 5 | 5 | 3000 | 6400 | In Stock |  | 1kA@32V Blade Fuse 3A 32V Fuses RoHS | Exact Matches | https://www.lcsc.com/product-detail/C151092.html
 |  |  |  |  |  | 303 | 5 |  |  | 0297010.WXNV | Littelfuse | 5 | 0.0873 | 0.44 | C151094 | - | 5 | 5 | 3000 | 18715 | In Stock |  | 1kA@32V Blade Fuse 10A 32V Fuses RoHS | Exact Matches | https://www.lcsc.com/product-detail/C151094.html
 |  |  |  |  |  | 201 | 5 |  |  | PH2.54-2X8P-H25 | JXTCONN | 5 | 0.0531 | 0.27 | C42431811 | Through Hole,P=2.54mm | 5 | 5 | 500 | 2800 | In Stock |  | Pin Header 16 Position 2.54mm Pitch Dual Row Through Hole -40℃~+105℃ | Exact Matches | https://www.lcsc.com/product-detail/C42431811.html
 |  |  |  |  |  | 202 | 5 |  |  | GPHA204-0502A001A1AC | GREENCONN | 5 | 0.2290 | 1.15 | C7434489 | Through Hole,P=2.54mm | 5 | 5 | 30 | 30 | In Stock |  | IDC Header 2 2.54mm -40℃~+105℃ 5 3A 2.54mm Through Hole,P=2.54mm Headers, Male Pins RoHS | Exact Matches | https://www.lcsc.com/product-detail/C7434489.html
 |  |  |  |  |  | 201 | 5 |  |  | -(The data has been deleted.) | - | - | - | - | - | - | - | - | - | - | - | - | - | -
 |  |  |  |  |  | 202 | 5 |  |  | -(The data has been deleted.) | - | - | - | - | - | - | - | - | - | - | - | - | - | -
 |  |  |  |  |  | 107 | 100 |  |  | RC0603FR-075K49L | YAGEO | 100 | 0.0007 | 0.07 | C188263 | 0603 | 100 | 100 | 5000 | 7000 | In Stock |  | 5.49kΩ 100mW 75V Thick Film Resistor ±100ppm/℃ ±1% 0603 Chip Resistor - Surface Mount RoHS | Exact Matches | https://www.lcsc.com/product-detail/C188263.html

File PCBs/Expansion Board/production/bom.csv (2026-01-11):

Designator | Footprint | Quantity | Value | LCSC Part #
J1, J2 | PinHeader_2x08_P2.54mm_Vertical | 2 | Conn_02x08_Odd_Even
J3, J4 | IDC-Header_2x05_P2.54mm_Vertical | 2 | Conn_02x05_Odd_Even
R1, R2 | 0603 | 2 | 10k

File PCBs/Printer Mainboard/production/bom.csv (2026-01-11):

Designator | Footprint | Quantity | Value | LCSC Part #
C1, C11, C12, C13, C14, C16, C18, C19, C20, C21, C22, C23, C24, C25, C26, C31, C32, C33, C34, C46, C47, C49, C50, C52, C53, C55, C56, C58, C59, C61, C62, C63, C64, C65, C66, C67, C68, C69, C70, C76, C77, C78, C79, C80, C81, C83, C85, C86, C87, C93, C94, C95 | 0603 | 52 | 100n
C10, C15, C17, C2, C41, C42, C43, C44, C45, C82, C9 | 0805 | 11 | 4μ7
C27, C28, C48, C51, C54, C57, C60 | CP_Elec_10x10 | 7 | 100μ
C29, C30 | CP_Elec_6.3x5.8 | 2 | 10μ
C3, C5 | 0805 | 2 | 470n 10V
C35 | 0603 | 1 | 10n
C36, C37, C38, C39, C40 | 0603 | 5 | 470n
C4 | CP_EIA-7343-43_Kemet-X | 1 | 220μ 10V
C6 | 1210 | 1 | 470n 100V
C7 | 1210 | 1 | 4μ7 100V
C71, C72, C73, C74, C75 | 0603 | 5 | 22n
C8 | 0603 | 1 | 2μ2 16V
C84, C88 | 0603 | 2 | 1μ
C89, C90 | 0603 | 2 | 8pF
C91, C92 | 0603 | 2 | 2μ2
D1, D26 | 0603 | 2 | LED_R
D10, D11, D6, D7 | 0603 | 4 | LED_B
D12, D5, D8, D9 | DIOM5436X250N | 4 | SMBJ64A
D13, D16, D19, D22 | 0603 | 4 | LED_YG
D14, D17, D20, D23 | D_SOD-323 | 4 | 1N5819
D15, D18, D21, D24, D27 | D_SOD-523 | 5 | 1N4148
D2 | D_SOD-123F | 1 | DSK24L
D25, D28 | D_SOD-523 | 2 | BAT54KFILM
D3, D4 | 0603 | 2 | LED_G
F1, F2 | FUSE-TH_4P-L16.0-W6.7 | 2 | XF-508P-B-B | C19727305
IC1 | QFN50P400X600X80-31N-D | 1 | LM76005RNPR
J1 | USB-A-TH_USB-302-T | 1 | USB_A
J10, J7, J8, J9 | CONN-TH_2P-P5.08_2EDG-5.08-2AW | 4 | Conn_01x02
J11, J12 | PinSocket_2x08_P2.54mm_Vertical | 2 | Conn_02x08_Odd_Even
J13, J14, J15 | PinSocket_1x04_P2.54mm_Vertical | 3 | Conn_01x04
J16, J17, J18, J19 | JST_XH_B3B-XH-A_1x03_P2.50mm_Vertical | 4 | Conn_01x03
J2 | USB-C_SMD-TYPE-C-31-M-12_1 | 1 | USB_C_Receptacle_USB2.0_14P
J20, J21 | CONN-TH_63849-1 | 2 | Faston
J22 | CONN-TH_DIN-422 | 1 | Mini-DIN-4
J23 | CONN-TH_MKDS3-2-5.08 | 1 | Conn_01x02
J24, J25 | PinHeader_1x02_P2.54mm_Vertical | 2 | Conn_01x02
J26, J27, J28, J29, J30 | JST_XH_B4B-XH-A_1x04_P2.50mm_Vertical | 5 | Conn_01x04
J3, J33, J36, J39, J4, J5, J6 | JST_XH_B2B-XH-A_1x02_P2.50mm_Vertical | 7 | Conn_01x02
J31 | PinHeader_1x06_P2.54mm_Vertical | 1 | Conn_01x06_Pin
J32, J35, J38 | PinSocket_1x03_P2.54mm_Vertical | 3 | Conn_01x03
J34, J37, J40 | PinSocket_1x02_P2.54mm_Vertical | 3 | Conn_01x02
K1 | Relay_SPST_Omron_G2RL-1A-E | 1 | G2RL-1A-E
L1 | L_Vishay_IHLP-4040 | 1 | 6.8μ
Q1, Q2, Q3, Q4 | NVMFS5C460NWFT1G | 4 | NVMFWS4D5N08XT1G
Q5, Q6, Q7, Q8 | SOT-23 | 4 | BC817
Q9 | SOT-23 | 1 | BC807
R1 | 0603 | 1 | 47k
R10, R12, R14, R16, R73 | 0603 | 5 | 4k7
R11, R13, R15, R17, R51, R53, R55, R72 | 0603 | 8 | 1k
R18, R19, R26, R27 | 0603 | 4 | 430R
R2, R52 | 0603 | 2 | 620R
R20, R22, R28, R30 | 0603 | 4 | 100R
R21, R23, R29, R31 | 0805 | 4 | 10R
R24, R25, R32, R33, R7, R8 | 0603 | 6 | 100k
R3, R4 | 0603 | 2 | 5k1
R34, R38, R42, R46 | 0603 | 4 | 536R
R35, R39, R43, R47, R54, R6 | 0603 | 6 | 470R
R36, R37, R40, R41, R44, R45, R48, R49 | 0603 | 8 | 1k8
R5 | 0603 | 1 | 120R
R50, R71 | 0603 | 2 | 10k
R56, R57, R58, R59, R60 | 0603 | 5 | 10R
R61, R62, R63, R64, R65, R66, R67, R68, R69, R70 | 1206 | 10 | 0.120R
R9 | 0603 | 1 | 24k9
S1 | SOT95P280X145-5N | 1 | STMPS2141STR
SW1 | SW-TH_SDDJF31100 | 1 | SW_SPST
SW2, SW3 | B3F3120 | 2 | SW_Push
U1 | SOT-23-6 | 1 | USBLC6-2SC6
U10, U11, U7, U8, U9 | TQFP-48-1EP_7x7mm_P0.5mm_EP5x5mm_ThermalVias | 5 | TMC2130-TA
U12 | LQFP-100_14x14mm_P0.5mm | 1 | STM32H743VITx
U2 | SOT-223-3_TabPin2 | 1 | AP7361C-33E
U3, U4 | SOIC-8_3.9x4.9mm_P1.27mm | 2 | TC4427xOA
U5 | TSSOP-14_4.4x5mm_P0.65mm | 1 | SN74LV4T125
U6 | SOIC-8_3.9x4.9mm_P1.27mm | 1 | NE555D
Y1 | Crystal_SMD_3225-4Pin_3.2x2.5mm | 1 | 25MHz

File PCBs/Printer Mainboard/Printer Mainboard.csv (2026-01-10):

Reference | Qty | Value | DNP | Exclude from BOM | Exclude from Board | Footprint | Datasheet
C1,C11,C12,C13,C14,C16,C18,C19,C20,C21,C22,C23,C24,C25,C26,C31,C32,C33,C34,C46,C47,C49,C50,C52,C53,C55,C56,C58,C59,C61,C62,C63,C64,C65,C66,C67,C68,C69,C70,C76,C77,C78,C79,C80,C81,C83,C85,C86,C87,C93,C94,C95 | 52 | 100n |  |  |  | Capacitor_SMD:C_0603_1608Metric | ~
C2,C9,C10,C15,C17,C41,C42,C43,C44,C45,C82 | 11 | 4μ7 |  |  |  | Capacitor_SMD:C_0805_2012Metric | ~
C3,C5 | 2 | 470n 10V |  |  |  | Capacitor_SMD:C_0805_2012Metric | ~
C4 | 1 | 220μ 10V |  |  |  | Capacitor_Tantalum_SMD:CP_EIA-7343-43_Kemet-X | ~
C6 | 1 | 470n 100V |  |  |  | Capacitor_SMD:C_1210_3225Metric | ~
C7 | 1 | 4μ7 100V |  |  |  | Capacitor_SMD:C_1210_3225Metric | ~
C8 | 1 | 2μ2 16V |  |  |  | Capacitor_SMD:C_0603_1608Metric | ~
C27,C28,C48,C51,C54,C57,C60 | 7 | 100μ |  |  |  | Capacitor_SMD:CP_Elec_10x10 | ~
C29,C30 | 2 | 10μ |  |  |  | Capacitor_SMD:CP_Elec_6.3x5.8 | ~
C35 | 1 | 10n |  |  |  | Capacitor_SMD:C_0603_1608Metric | ~
C36,C37,C38,C39,C40 | 5 | 470n |  |  |  | Capacitor_SMD:C_0603_1608Metric | ~
C71,C72,C73,C74,C75 | 5 | 22n |  |  |  | Capacitor_SMD:C_0603_1608Metric | ~
C84,C88 | 2 | 1μ |  |  |  | Capacitor_SMD:C_0603_1608Metric | ~
C89,C90 | 2 | 8pF |  |  |  | Capacitor_SMD:C_0603_1608Metric | ~
C91,C92 | 2 | 2μ2 |  |  |  | Capacitor_SMD:C_0603_1608Metric | ~
D1,D26 | 2 | LED_R |  |  |  | LED_SMD:LED_0603_1608Metric | ~
D2 | 1 | DSK24L |  |  |  | Diode_SMD:D_SOD-123F | ~
D3,D4 | 2 | LED_G |  |  |  | LED_SMD:LED_0603_1608Metric | ~
D5,D8,D9,D12 | 4 | SMBJ64A |  |  |  | SamacSys_Parts:DIOM5436X250N | https://semtech.my.salesforce.com/sfc/p/E0000000JelG/a/RQ000008cm73/_XXCZXiaFZrSCT8msVUSeP9R8FW7FIaoaEDo5VeyxOY
D6,D7,D10,D11 | 4 | LED_B |  |  |  | LED_SMD:LED_0603_1608Metric | ~
D13,D16,D19,D22 | 4 | LED_YG |  |  |  | LED_SMD:LED_0603_1608Metric | ~
D14,D17,D20,D23 | 4 | 1N5819 |  |  |  | Diode_SMD:D_SOD-323 | ~
D15,D18,D21,D24,D27 | 5 | 1N4148 |  |  |  | Diode_SMD:D_SOD-523 | ~
D25,D28 | 2 | BAT54KFILM |  |  |  | Diode_SMD:D_SOD-523 | ~
F1,F2 | 2 | XF-508P-B-B |  |  |  | LCSC:FUSE-TH_4P-L16.0-W6.7
H1,H2,H3,H4 | 4 | MountingHole_Pad |  | Excluded from BOM |  | MountingHole:MountingHole_3.2mm_M3_Pad | ~
IC1 | 1 | LM76005RNPR |  |  |  | SamacSys_Parts:QFN50P400X600X80-31N-D | https://datasheet.datasheetarchive.com/originals/distributors/Datasheets_SAMA/d5c64775b80bf9ebe325fd747957355c.pdf
J1 | 1 | USB_A |  |  |  | LCSC:USB-A-TH_USB-302-T | ~
J2 | 1 | USB_C_Receptacle_USB2.0_14P |  |  |  | LCSC:USB-C_SMD-TYPE-C-31-M-12_1 | https://www.usb.org/sites/default/files/documents/usb_type-c.zip
J3,J4,J5,J6,J33,J36,J39 | 7 | Conn_01x02 |  |  |  | Connector_JST:JST_XH_B2B-XH-A_1x02_P2.50mm_Vertical | ~
J7,J8,J9,J10 | 4 | Conn_01x02 |  |  |  | LCSC:CONN-TH_2P-P5.08_2EDG-5.08-2AW | ~
J11,J12 | 2 | Conn_02x08_Odd_Even |  |  |  | Connector_PinSocket_2.54mm:PinSocket_2x08_P2.54mm_Vertical | ~
J13,J14,J15 | 3 | Conn_01x04 |  |  |  | Connector_PinSocket_2.54mm:PinSocket_1x04_P2.54mm_Vertical | ~
J16,J17,J18,J19 | 4 | Conn_01x03 |  |  |  | Connector_JST:JST_XH_B3B-XH-A_1x03_P2.50mm_Vertical | ~
J20,J21 | 2 | Faston |  |  |  | LCSC:CONN-TH_63849-1 | ~
J22 | 1 | Mini-DIN-4 |  |  |  | LCSC:CONN-TH_DIN-422 | http://service.powerdynamics.com/ec/Catalog17/Section%2011.pdf
J23 | 1 | Conn_01x02 |  |  |  | LCSC:CONN-TH_MKDS3-2-5.08 | ~
J24,J25 | 2 | Conn_01x02 |  |  |  | Connector_PinHeader_2.54mm:PinHeader_1x02_P2.54mm_Vertical | ~
J26,J27,J28,J29,J30 | 5 | Conn_01x04 |  |  |  | Connector_JST:JST_XH_B4B-XH-A_1x04_P2.50mm_Vertical | ~
J31 | 1 | Conn_01x06_Pin |  |  |  | Connector_PinHeader_2.54mm:PinHeader_1x06_P2.54mm_Vertical | ~
J32,J35,J38 | 3 | Conn_01x03 |  |  |  | Connector_PinSocket_2.54mm:PinSocket_1x03_P2.54mm_Vertical | ~
J34,J37,J40 | 3 | Conn_01x02 |  |  |  | Connector_PinSocket_2.54mm:PinSocket_1x02_P2.54mm_Vertical | ~
K1 | 1 | G2RL-1A-E |  |  |  | Relay_THT:Relay_SPST_Omron_G2RL-1A-E | https://omronfs.omron.com/en_US/ecb/products/pdf/en-g2rl.pdf
L1 | 1 | 6.8μ |  |  |  | Inductor_SMD:L_Vishay_IHLP-4040 | ~
Q1,Q2,Q3,Q4 | 4 | NVMFWS4D5N08XT1G |  |  |  | SamacSys_Parts:NVMFS5C460NWFT1G | https://www.onsemi.com/pub/Collateral/NVMFWS4D5N08X-D.PDF
Q5,Q6,Q7,Q8 | 4 | BC817 |  |  |  | Package_TO_SOT_SMD:SOT-23 | https://www.onsemi.com/pub/Collateral/BC818-D.pdf
Q9 | 1 | BC807 |  |  |  | Package_TO_SOT_SMD:SOT-23 | https://www.onsemi.com/pub/Collateral/BC808-D.pdf
R1 | 1 | 47k |  |  |  | Resistor_SMD:R_0603_1608Metric | ~
R2,R52 | 2 | 620R |  |  |  | Resistor_SMD:R_0603_1608Metric | ~
R3,R4 | 2 | 5k1 |  |  |  | Resistor_SMD:R_0603_1608Metric | ~
R5 | 1 | 120R |  |  |  | Resistor_SMD:R_0603_1608Metric | ~
R6,R35,R39,R43,R47,R54 | 6 | 470R |  |  |  | Resistor_SMD:R_0603_1608Metric | ~
R7,R8,R24,R25,R32,R33 | 6 | 100k |  |  |  | Resistor_SMD:R_0603_1608Metric | ~
R9 | 1 | 24k9 |  |  |  | Resistor_SMD:R_0603_1608Metric | ~
R10,R12,R14,R16,R73 | 5 | 4k7 |  |  |  | Resistor_SMD:R_0603_1608Metric | ~
R11,R13,R15,R17,R51,R53,R55,R72 | 8 | 1k |  |  |  | Resistor_SMD:R_0603_1608Metric | ~
R18,R19,R26,R27 | 4 | 430R |  |  |  | Resistor_SMD:R_0603_1608Metric | ~
R20,R22,R28,R30 | 4 | 100R |  |  |  | Resistor_SMD:R_0603_1608Metric | ~
R21,R23,R29,R31 | 4 | 10R |  |  |  | Resistor_SMD:R_0805_2012Metric | ~
R34,R38,R42,R46 | 4 | 536R |  |  |  | Resistor_SMD:R_0603_1608Metric | ~
R36,R37,R40,R41,R44,R45,R48,R49 | 8 | 1k8 |  |  |  | Resistor_SMD:R_0603_1608Metric | ~
R50,R71 | 2 | 10k |  |  |  | Resistor_SMD:R_0603_1608Metric | ~
R56,R57,R58,R59,R60 | 5 | 10R |  |  |  | Resistor_SMD:R_0603_1608Metric | ~
R61,R62,R63,R64,R65,R66,R67,R68,R69,R70 | 10 | 0.120R |  |  |  | Resistor_SMD:R_1206_3216Metric | ~
S1 | 1 | STMPS2141STR |  |  |  | SamacSys_Parts:SOT95P280X145-5N | https://www.st.com/resource/en/datasheet/stmps2141.pdf
SW1 | 1 | SW_SPST |  |  |  | LCSC:SW-TH_SDDJF31100 | ~
SW2,SW3 | 2 | SW_Push |  |  |  | SamacSys_Parts:B3F3120 | ~
U1 | 1 | USBLC6-2SC6 |  |  |  | Package_TO_SOT_SMD:SOT-23-6 | https://www.st.com/resource/en/datasheet/usblc6-2.pdf
U2 | 1 | AP7361C-33E |  |  |  | Package_TO_SOT_SMD:SOT-223-3_TabPin2 | https://www.diodes.com/assets/Datasheets/AP7361C.pdf
U3,U4 | 2 | TC4427xOA |  |  |  | Package_SO:SOIC-8_3.9x4.9mm_P1.27mm | https://ww1.microchip.com/downloads/en/DeviceDoc/20001422G.pdf
U5 | 1 | SN74LV4T125 |  |  |  | Package_SO:TSSOP-14_4.4x5mm_P0.65mm | https://www.ti.com/lit/ds/symlink/sn74lv4t125.pdf
U6 | 1 | NE555D |  |  |  | Package_SO:SOIC-8_3.9x4.9mm_P1.27mm | http://www.ti.com/lit/ds/symlink/ne555.pdf
U7,U8,U9,U10,U11 | 5 | TMC2130-TA |  |  |  | Package_QFP:TQFP-48-1EP_7x7mm_P0.5mm_EP5x5mm_ThermalVias | http://www.trinamic.com/fileadmin/assets/Products/ICs_Documents/TMC2130_datasheet.pdf
U12 | 1 | STM32H743VITx |  |  |  | Package_QFP:LQFP-100_14x14mm_P0.5mm | https://www.st.com/resource/en/datasheet/stm32h743vi.pdf
Y1 | 1 | 25MHz |  |  |  | Crystal:Crystal_SMD_3225-4Pin_3.2x2.5mm | ~

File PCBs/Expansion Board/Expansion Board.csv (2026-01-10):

Reference | Qty | Value | DNP | Exclude from BOM | Exclude from Board | Footprint | Datasheet
J1,J2 | 2 | Conn_02x08_Odd_Even |  |  |  | Connector_PinHeader_2.54mm:PinHeader_2x08_P2.54mm_Vertical | ~
J3,J4 | 2 | Conn_02x05_Odd_Even |  |  |  | Connector_IDC:IDC-Header_2x05_P2.54mm_Vertical | ~
R1,R2 | 2 | 10k |  |  |  | Resistor_SMD:R_0603_1608Metric | ~

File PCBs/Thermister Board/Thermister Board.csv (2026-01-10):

Reference | Qty | Value | DNP | Exclude from BOM | Exclude from Board | Footprint | Datasheet
C1,C2,C3,C4,C6 | 5 | 100n |  |  |  | Capacitor_SMD:C_0603_1608Metric | ~
C5 | 1 | 1µ |  |  |  | Capacitor_SMD:C_0603_1608Metric | ~
J1,J4 | 2 | Conn_01x03 |  |  |  | Connector_PinHeader_2.54mm:PinHeader_1x03_P2.54mm_Vertical | ~
J2,J3 | 2 | Conn_01x02 |  |  |  | Connector_PinHeader_2.54mm:PinHeader_1x02_P2.54mm_Vertical | ~
JP1 | 1 | SolderJumper |  | Excluded from BOM |  | Jumper:SolderJumper-3_P1.3mm_Open_RoundedPad1.0x1.5mm_NumberLabels | ~
R1,R2 | 2 | 2k2 |  |  |  | Resistor_SMD:R_0603_1608Metric | ~
R3,R4,R8 | 3 | 10k |  |  |  | Resistor_SMD:R_0603_1608Metric | ~
R5 | 1 | 5k49 |  |  |  | Resistor_SMD:R_0603_1608Metric | ~
R6 | 1 | 100R |  |  |  | Resistor_SMD:R_0603_1608Metric | ~
R7 | 1 | 100k |  |  |  | Resistor_SMD:R_0603_1608Metric | ~
U1 | 1 | INA826AIDRGR |  |  |  | Package_SON:WSON-8-1EP_3x3mm_P0.5mm_EP1.45x2.4mm_ThermalVias

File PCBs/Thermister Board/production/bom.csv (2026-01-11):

Designator | Footprint | Quantity | Value | LCSC Part #
C1_12, C1_11, C1_10, C1_9, C1_8, C1_7, C1_6, C1_5, C1_4, C1_3, C1_2, C1, C2_12, C2_11, C2_10, C2_9, C2_8, C2_7, C2_6, C2_5, C2_4, C2_3, C2_2, C2, C3_12, C3_11, C3_10, C3_9, C3_8, C3_7, C3_6, C3_5, C3_4, C3_3, C3_2, C3, C4_12, C4_11, C4_10, C4_9, C4_8, C4_7, C4_6, C4_5, C4_4, C4_3, C4_2, C4, C6_12, C6_11, C6_10, C6_9, C6_8, C6_7, C6_6, C6_5, C6_4, C6_3, C6_2, C6 | 0603 | 60 | 100n
C5_12, C5_11, C5_10, C5_9, C5_8, C5_7, C5_6, C5_5, C5_4, C5_3, C5_2, C5 | 0603 | 12 | 1µ
J1_12, J1_11, J1_10, J1_9, J1_8, J1_7, J1_6, J1_5, J1_4, J1_3, J1_2, J1, J4_12, J4_11, J4_10, J4_9, J4_8, J4_7, J4_6, J4_5, J4_4, J4_3, J4_2, J4 | PinHeader_1x03_P2.54mm_Vertical | 24 | Conn_01x03
J2_12, J2_11, J2_10, J2_9, J2_8, J2_7, J2_6, J2_5, J2_4, J2_3, J2_2, J2, J3_12, J3_11, J3_10, J3_9, J3_8, J3_7, J3_6, J3_5, J3_4, J3_3, J3_2, J3 | PinHeader_1x02_P2.54mm_Vertical | 24 | Conn_01x02
R1_12, R1_11, R1_10, R1_9, R1_8, R1_7, R1_6, R1_5, R1_4, R1_3, R1_2, R1, R2_12, R2_11, R2_10, R2_9, R2_8, R2_7, R2_6, R2_5, R2_4, R2_3, R2_2, R2 | 0603 | 24 | 2k2
R3_12, R3_11, R3_10, R3_9, R3_8, R3_7, R3_6, R3_5, R3_4, R3_3, R3_2, R3, R4_12, R4_11, R4_10, R4_9, R4_8, R4_7, R4_6, R4_5, R4_4, R4_3, R4_2, R4, R8_12, R8_11, R8_10, R8_9, R8_8, R8_7, R8_6, R8_5, R8_4, R8_3, R8_2, R8 | 0603 | 36 | 10k
R5_12, R5_11, R5_10, R5_9, R5_8, R5_7, R5_6, R5_5, R5_4, R5_3, R5_2, R5 | 0603 | 12 | 5k49
R6_12, R6_11, R6_10, R6_9, R6_8, R6_7, R6_6, R6_5, R6_4, R6_3, R6_2, R6 | 0603 | 12 | 100R
R7_12, R7_11, R7_10, R7_9, R7_8, R7_7, R7_6, R7_5, R7_4, R7_3, R7_2, R7 | 0603 | 12 | 100k
U1_12, U1_11, U1_10, U1_9, U1_8, U1_7, U1_6, U1_5, U1_4, U1_3, U1_2, U1 | WSON-8-1EP_3x3mm_P0.5mm_EP1.45x2.4mm_ThermalVias | 12 | INA826AIDRGR

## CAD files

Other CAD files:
3D/SCORPION MAX V1 Video.blend
3D/SCORPION MAX V1.blend

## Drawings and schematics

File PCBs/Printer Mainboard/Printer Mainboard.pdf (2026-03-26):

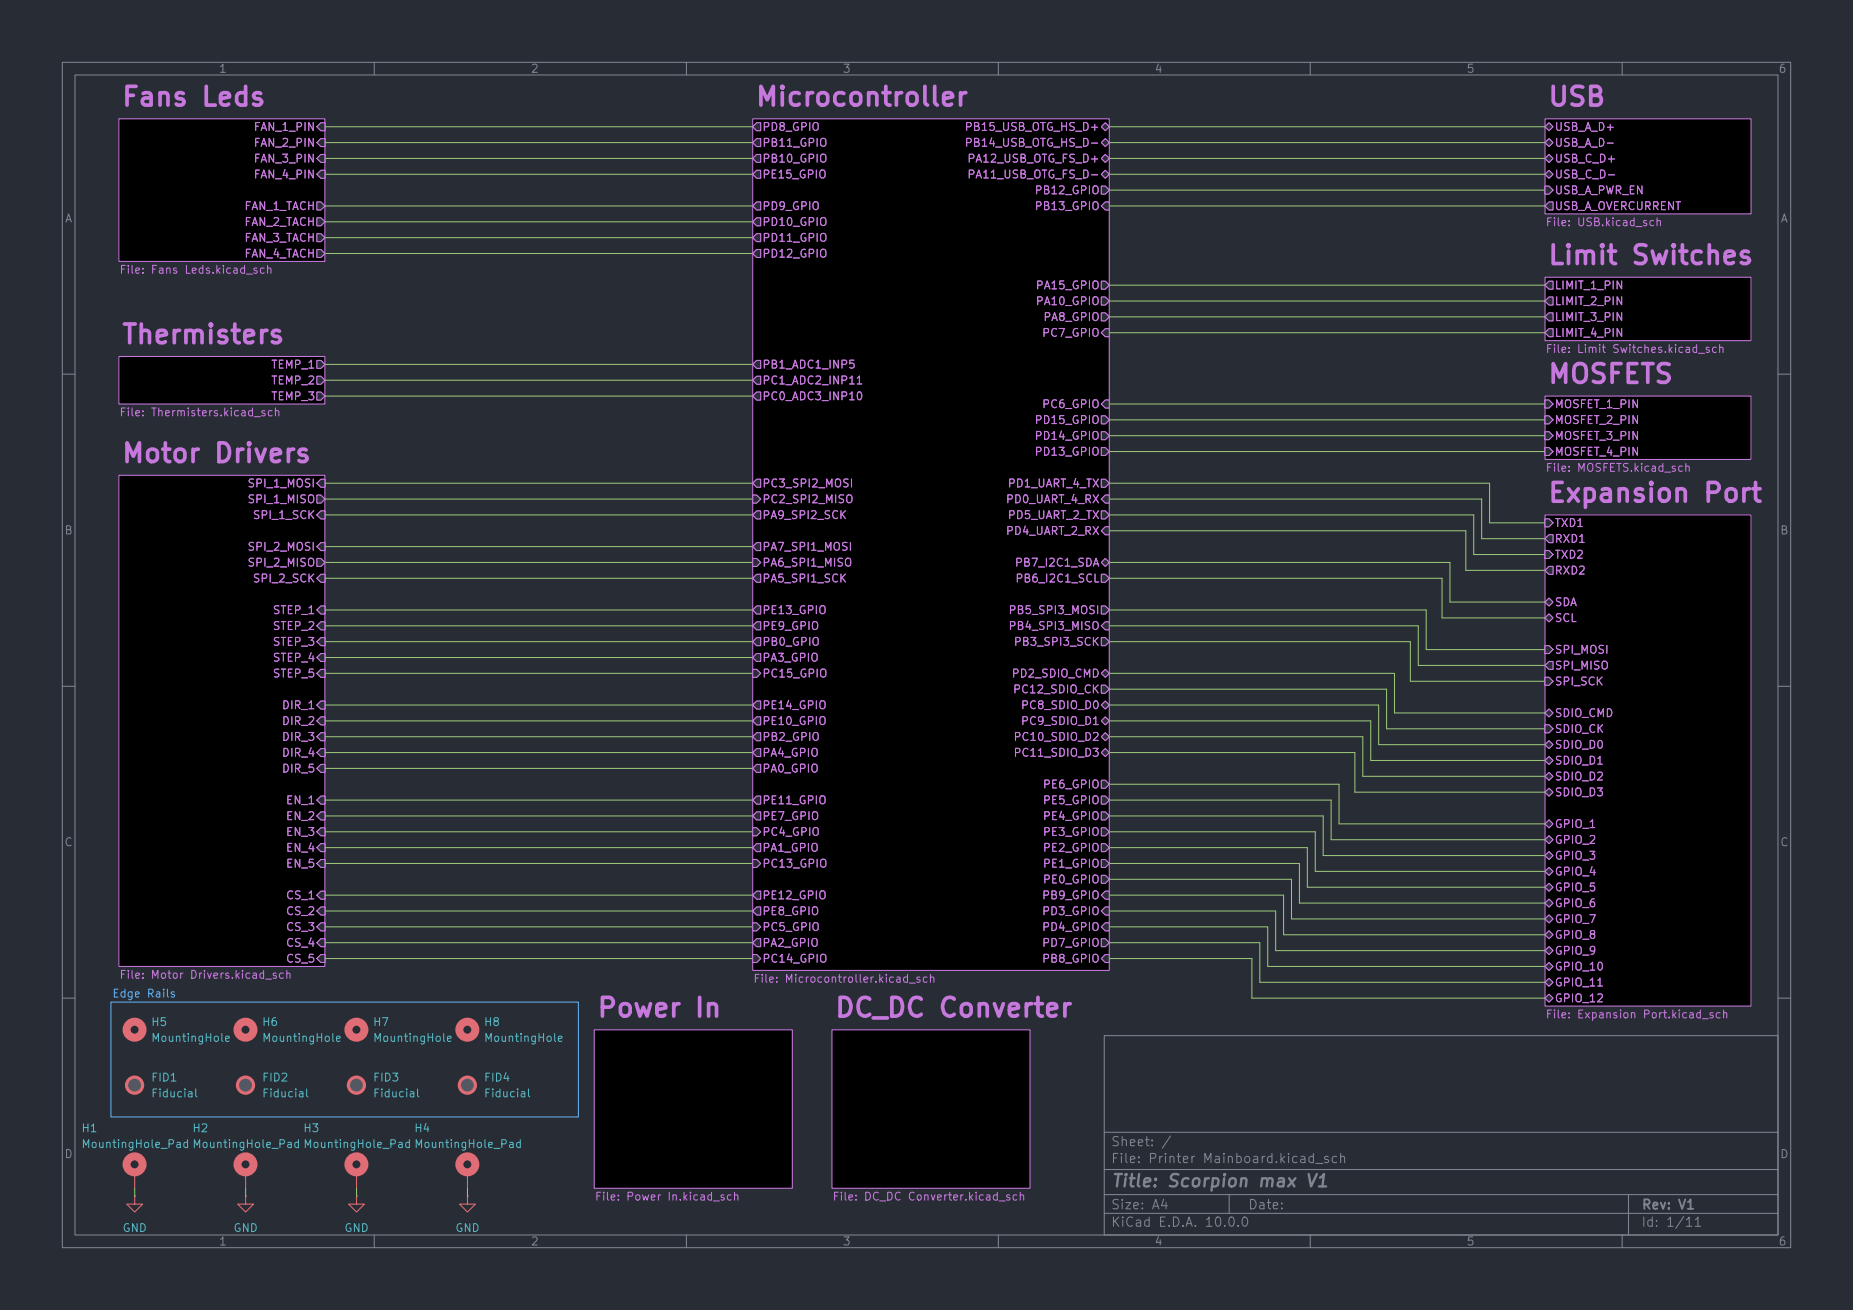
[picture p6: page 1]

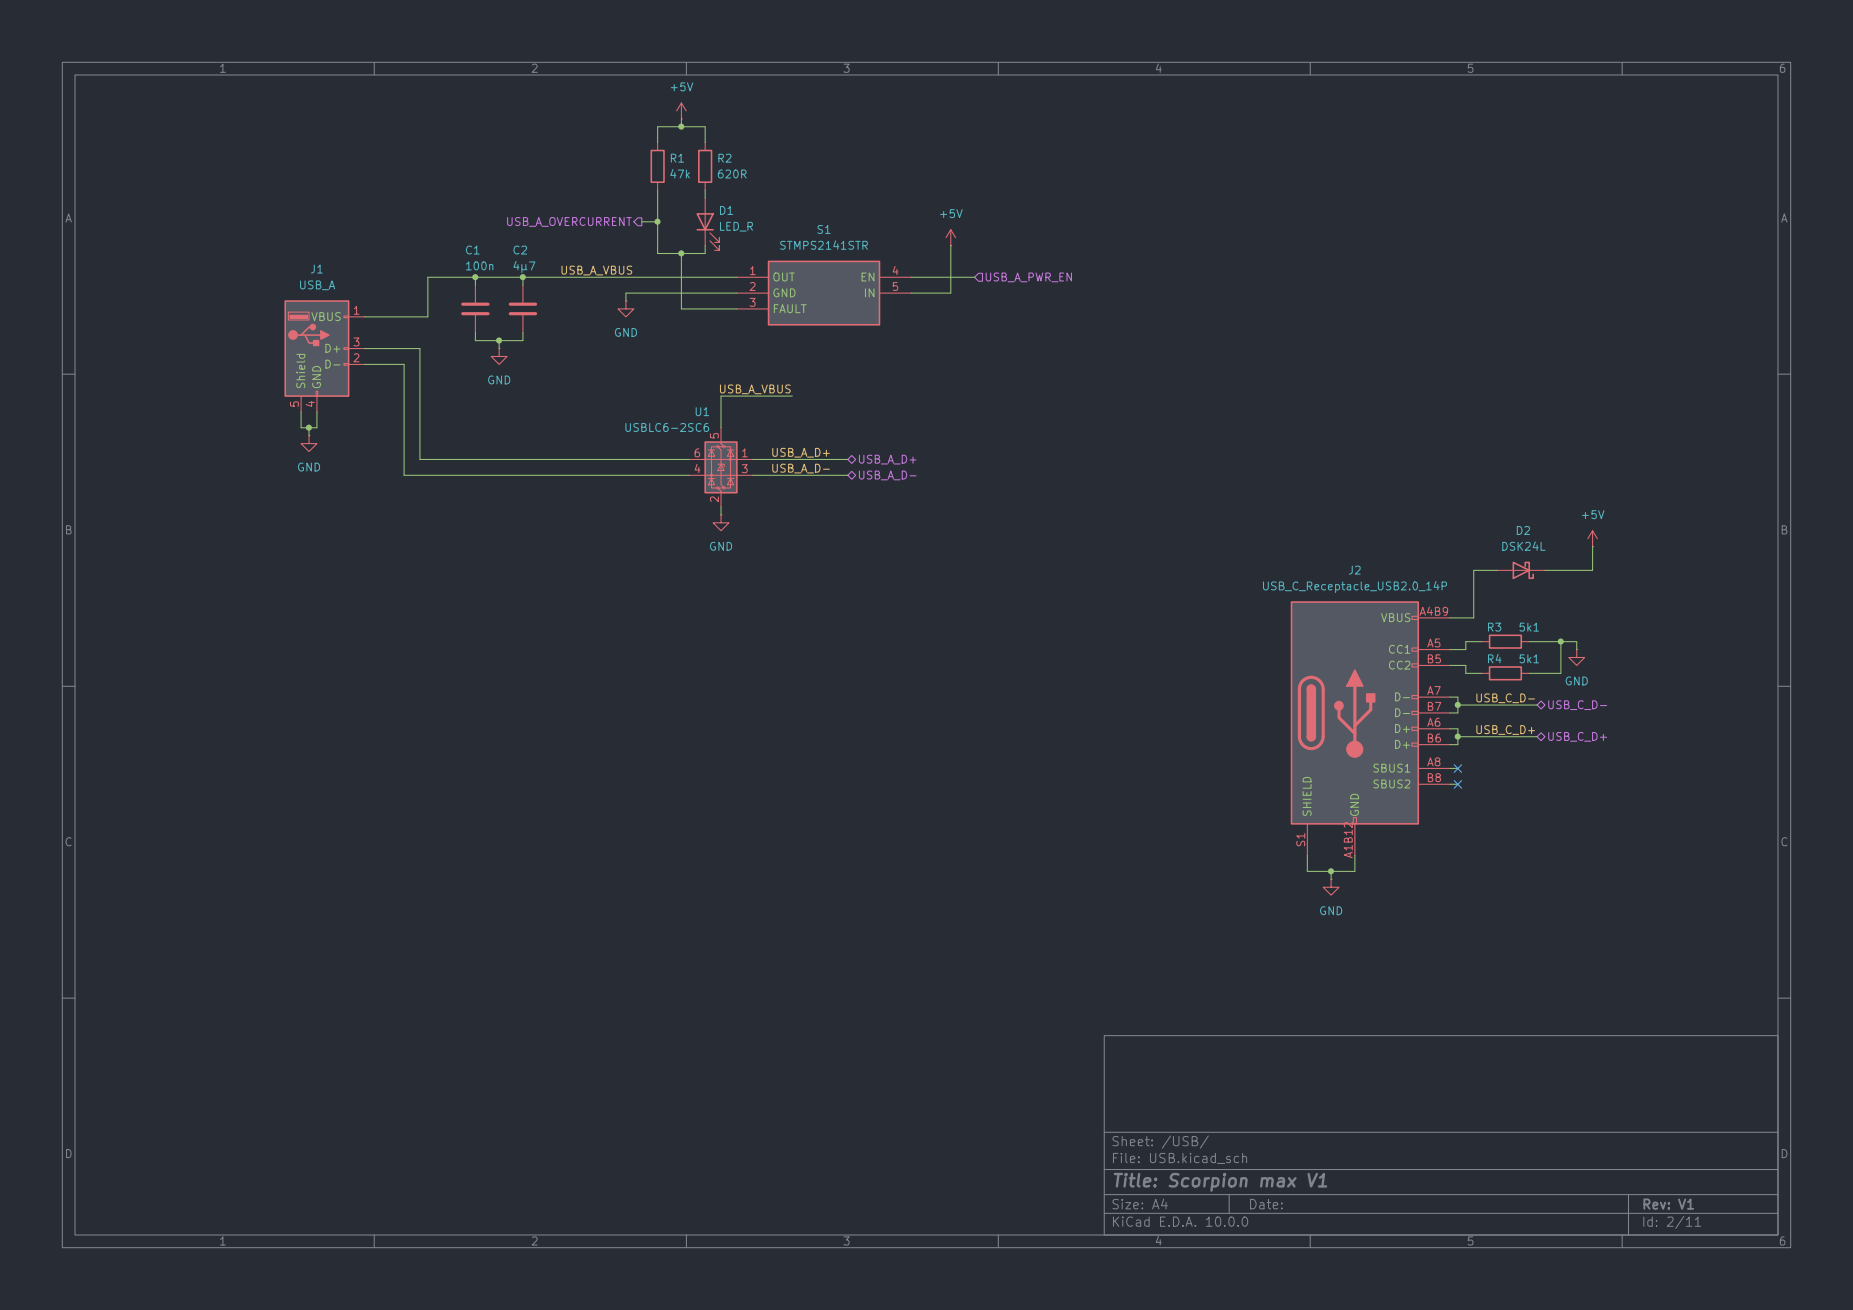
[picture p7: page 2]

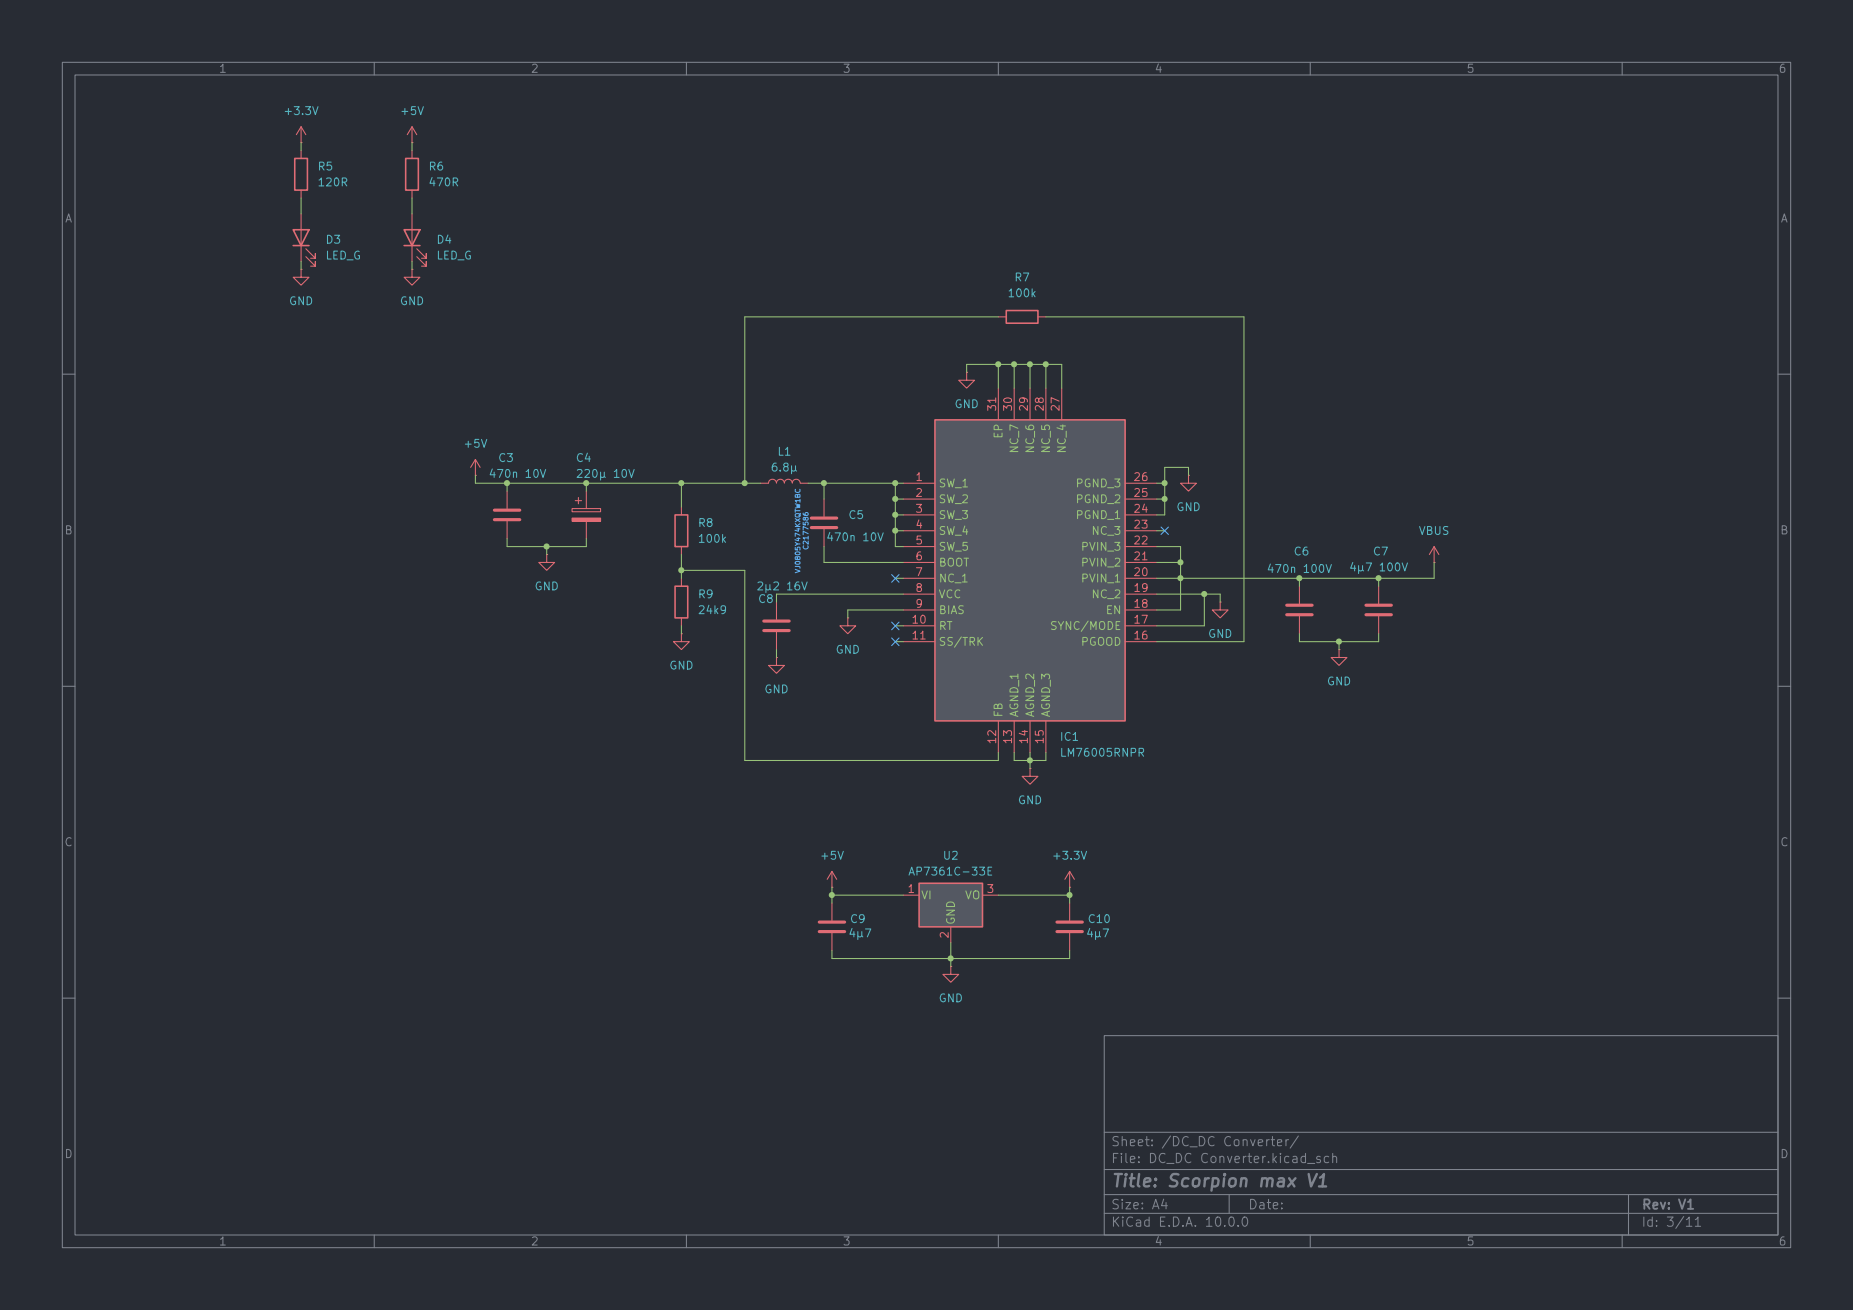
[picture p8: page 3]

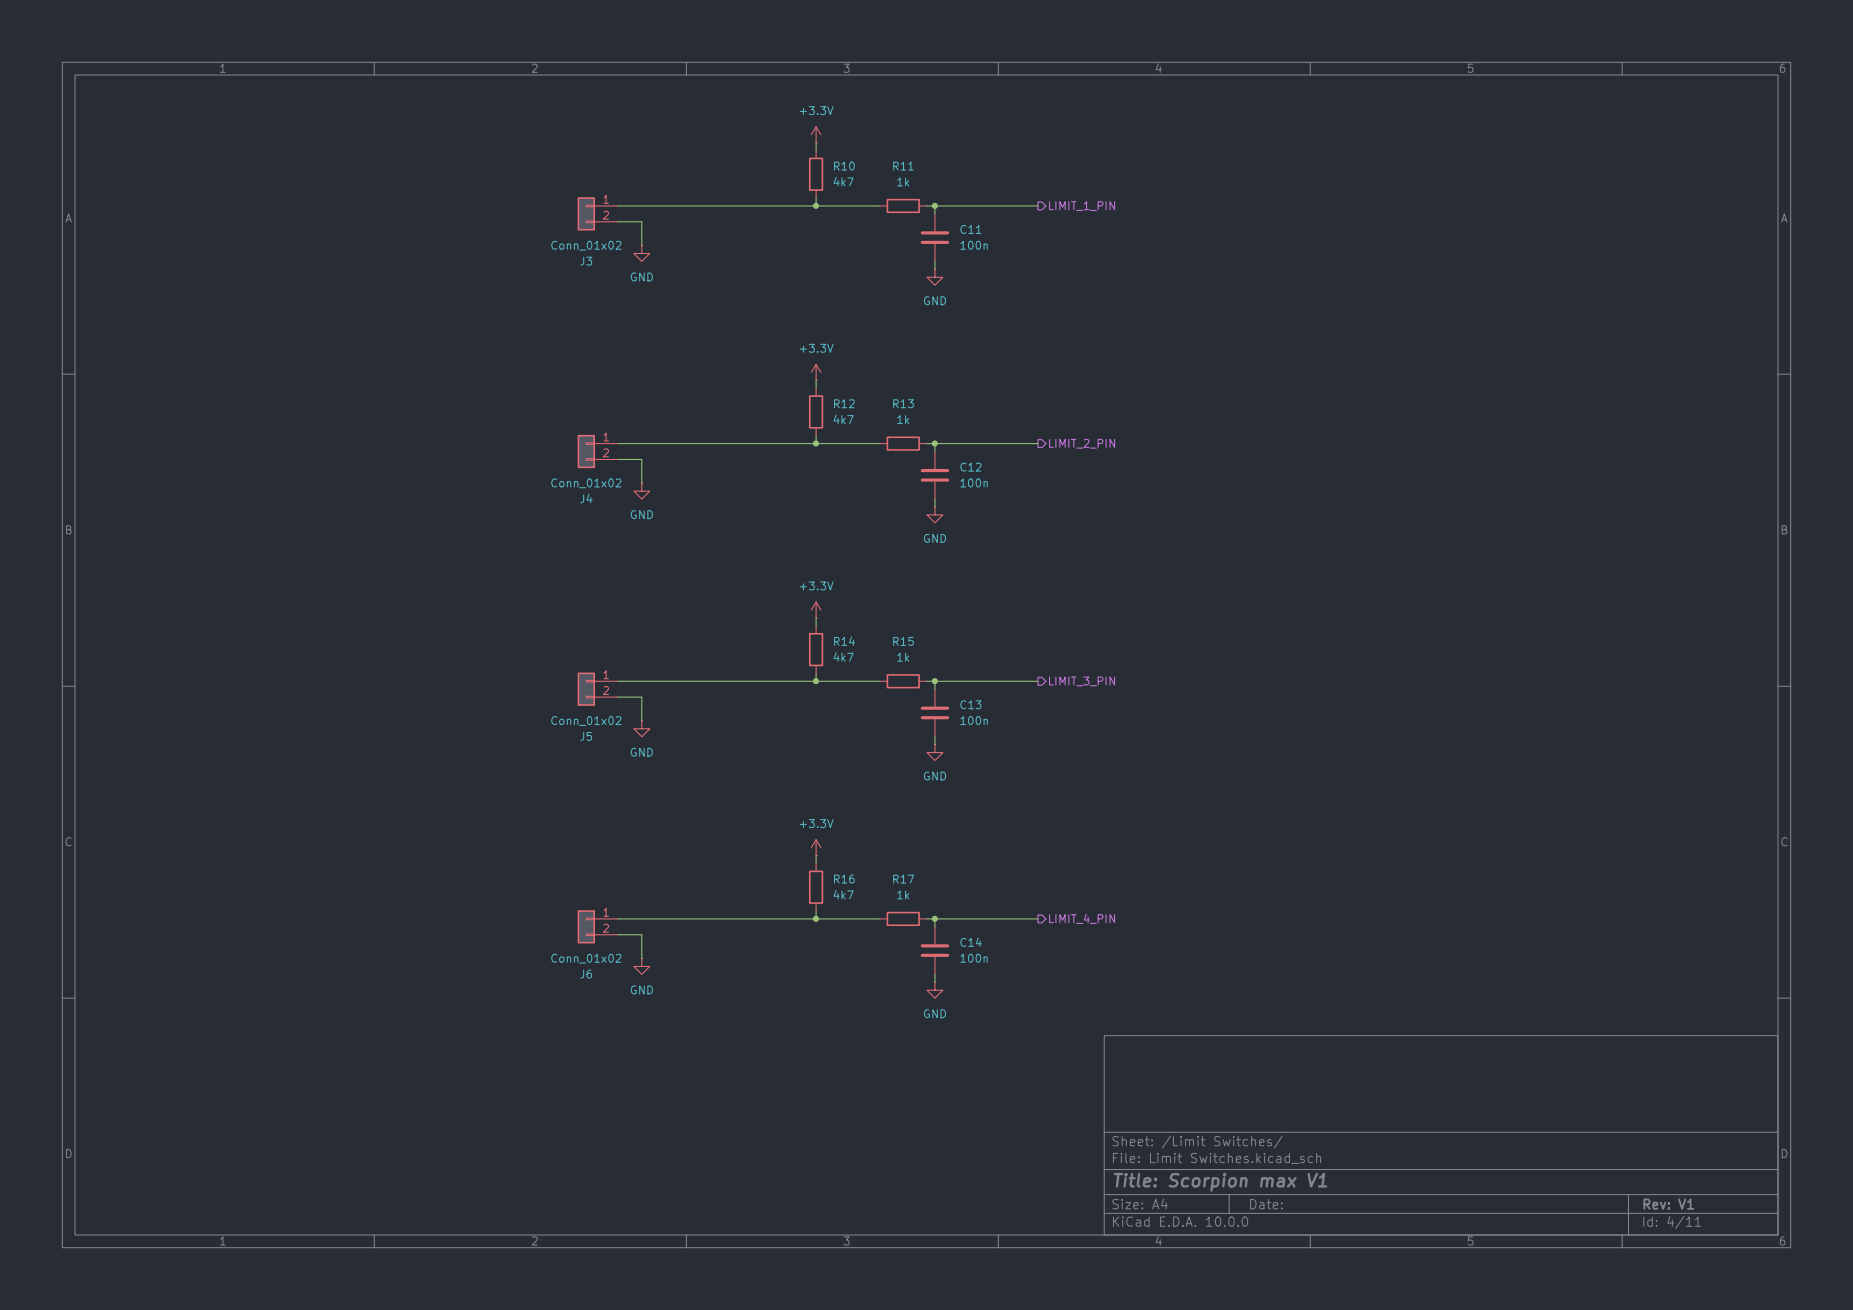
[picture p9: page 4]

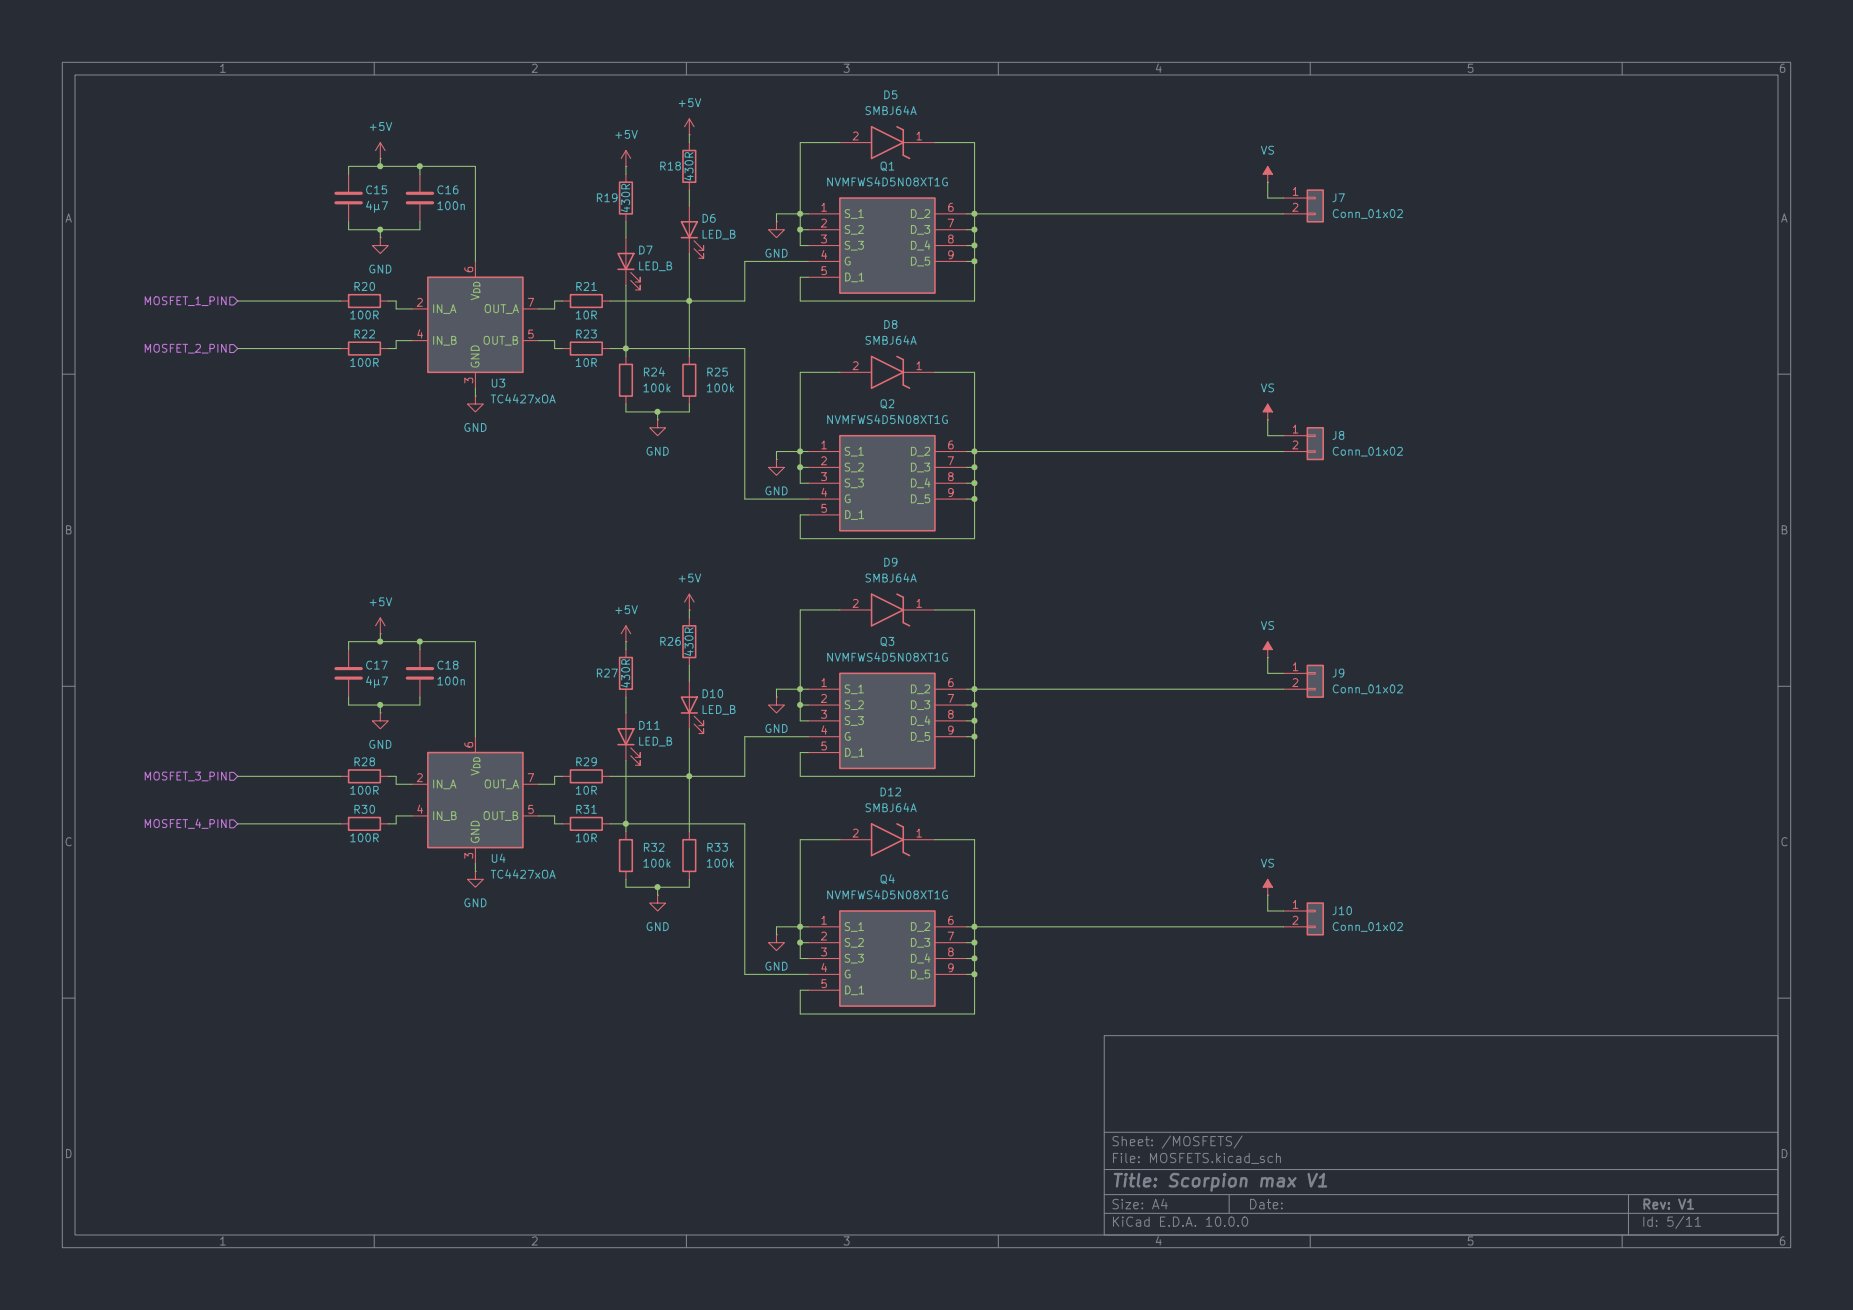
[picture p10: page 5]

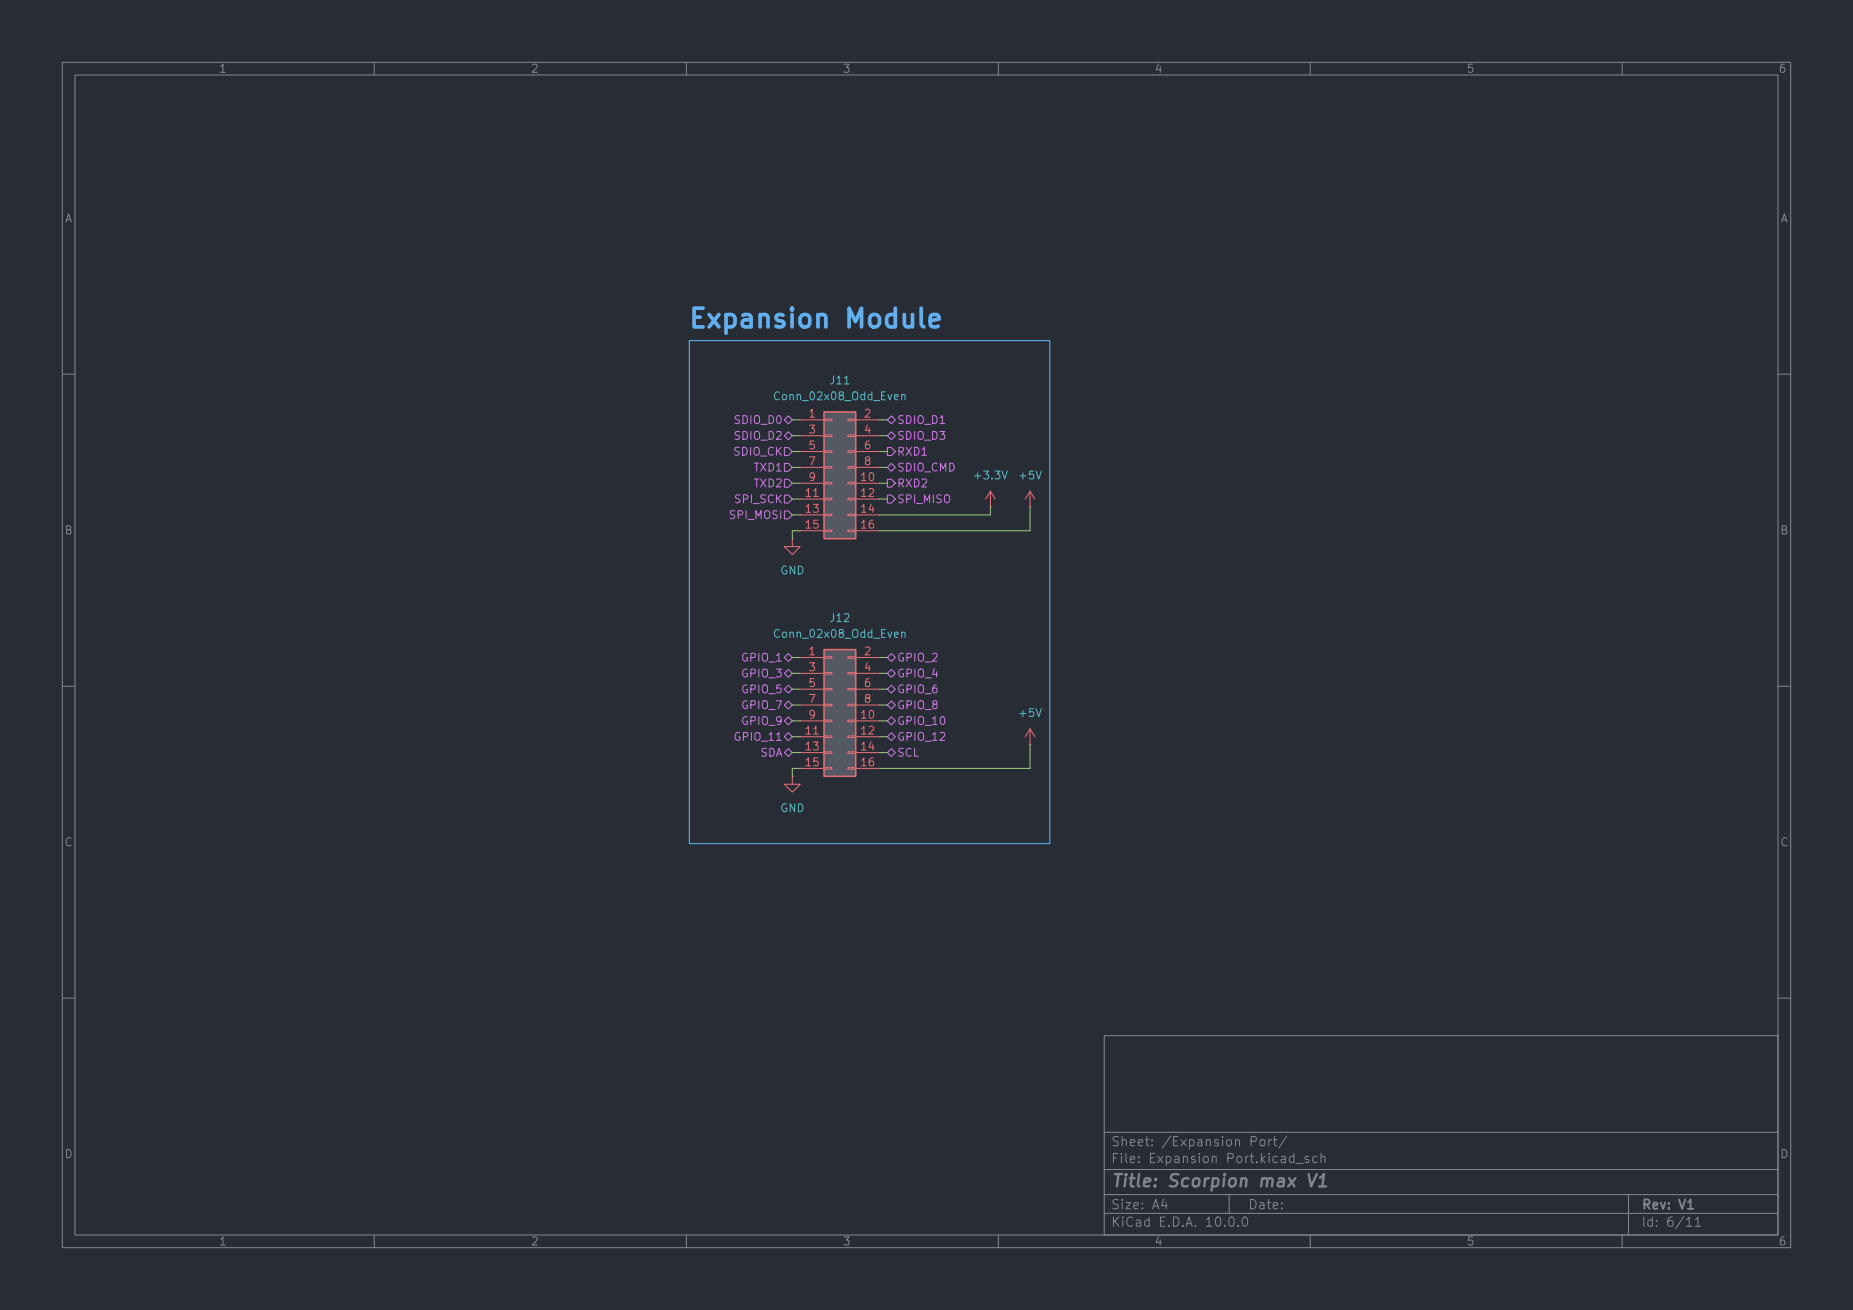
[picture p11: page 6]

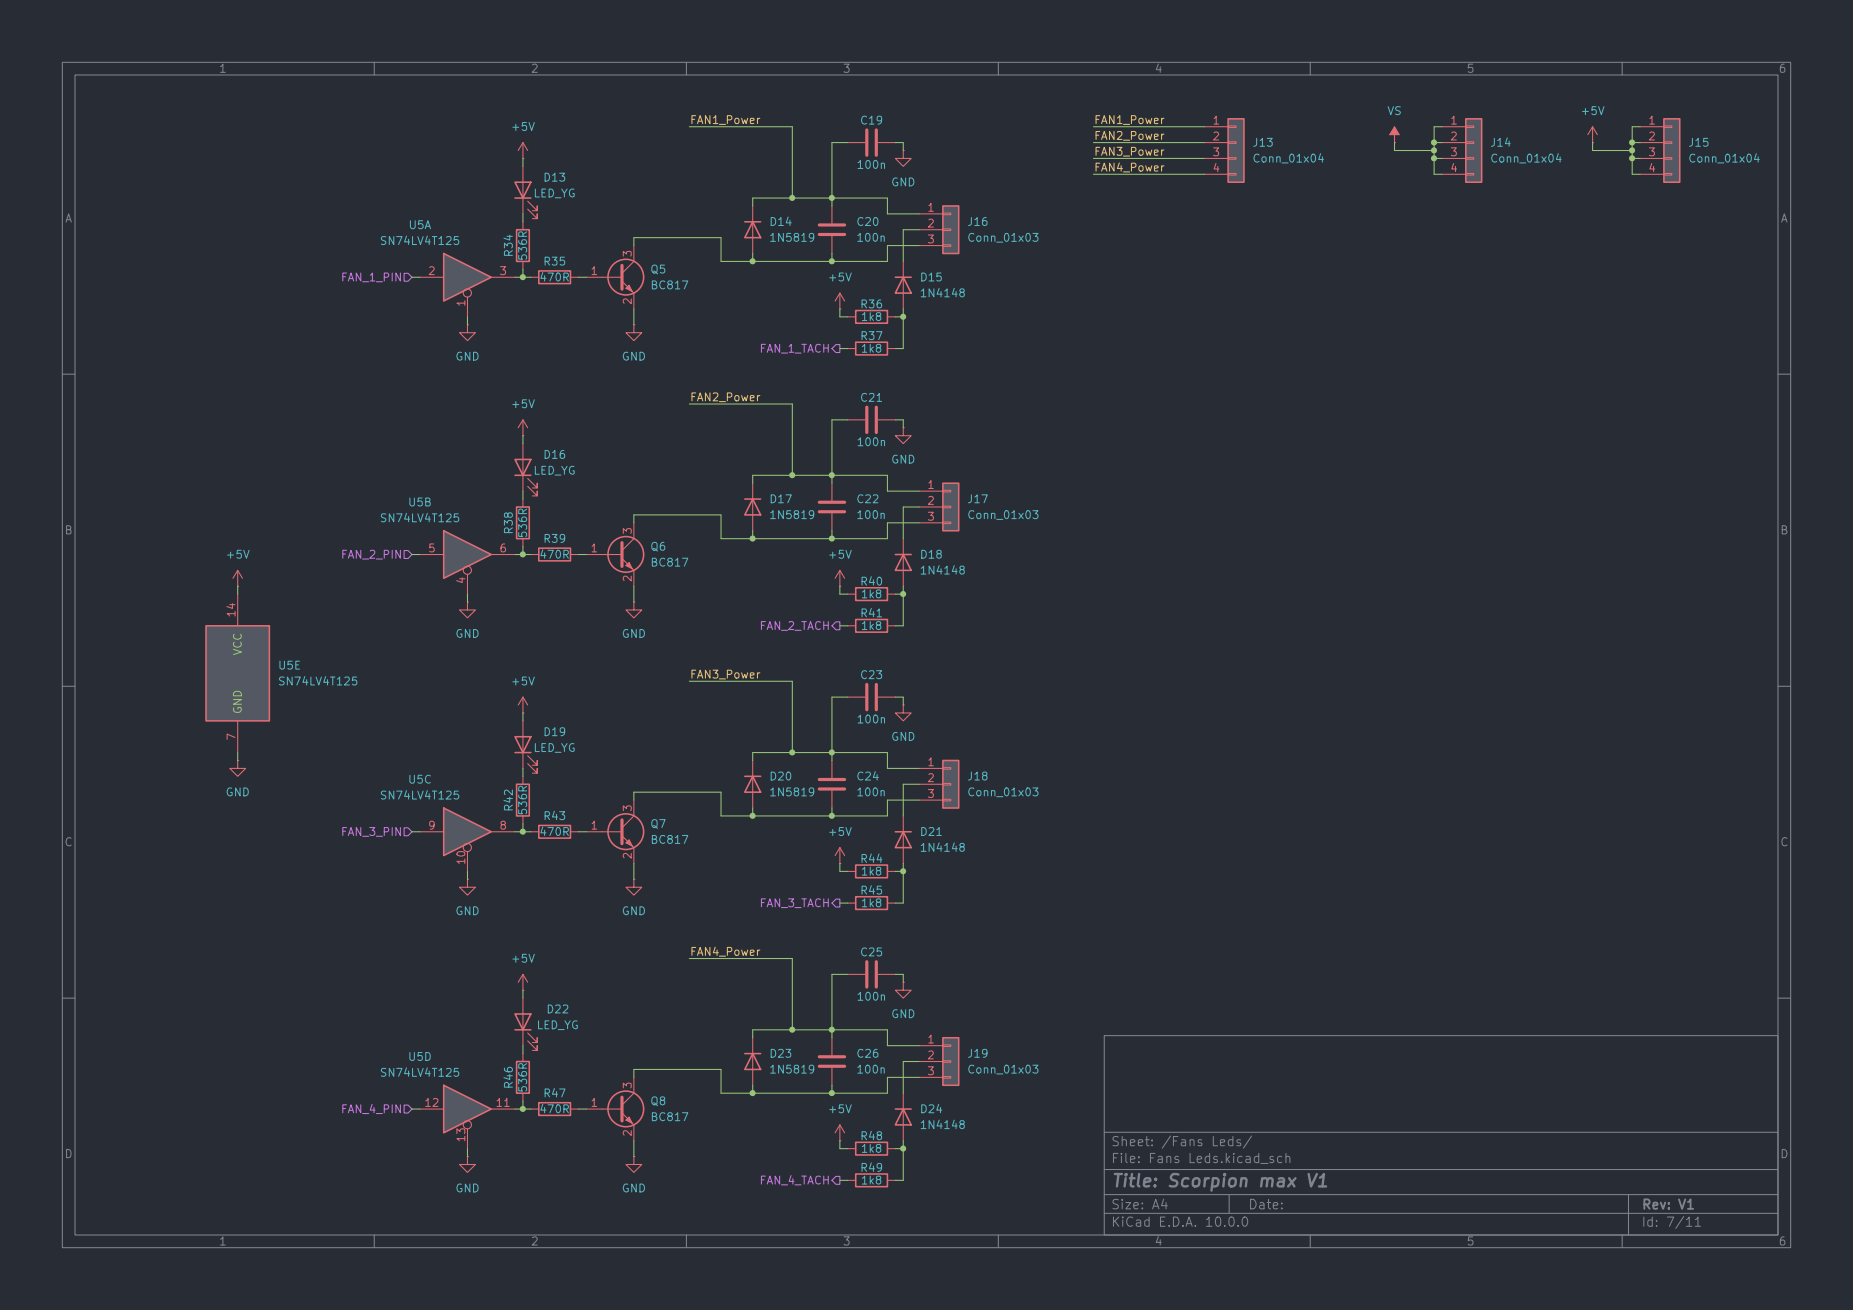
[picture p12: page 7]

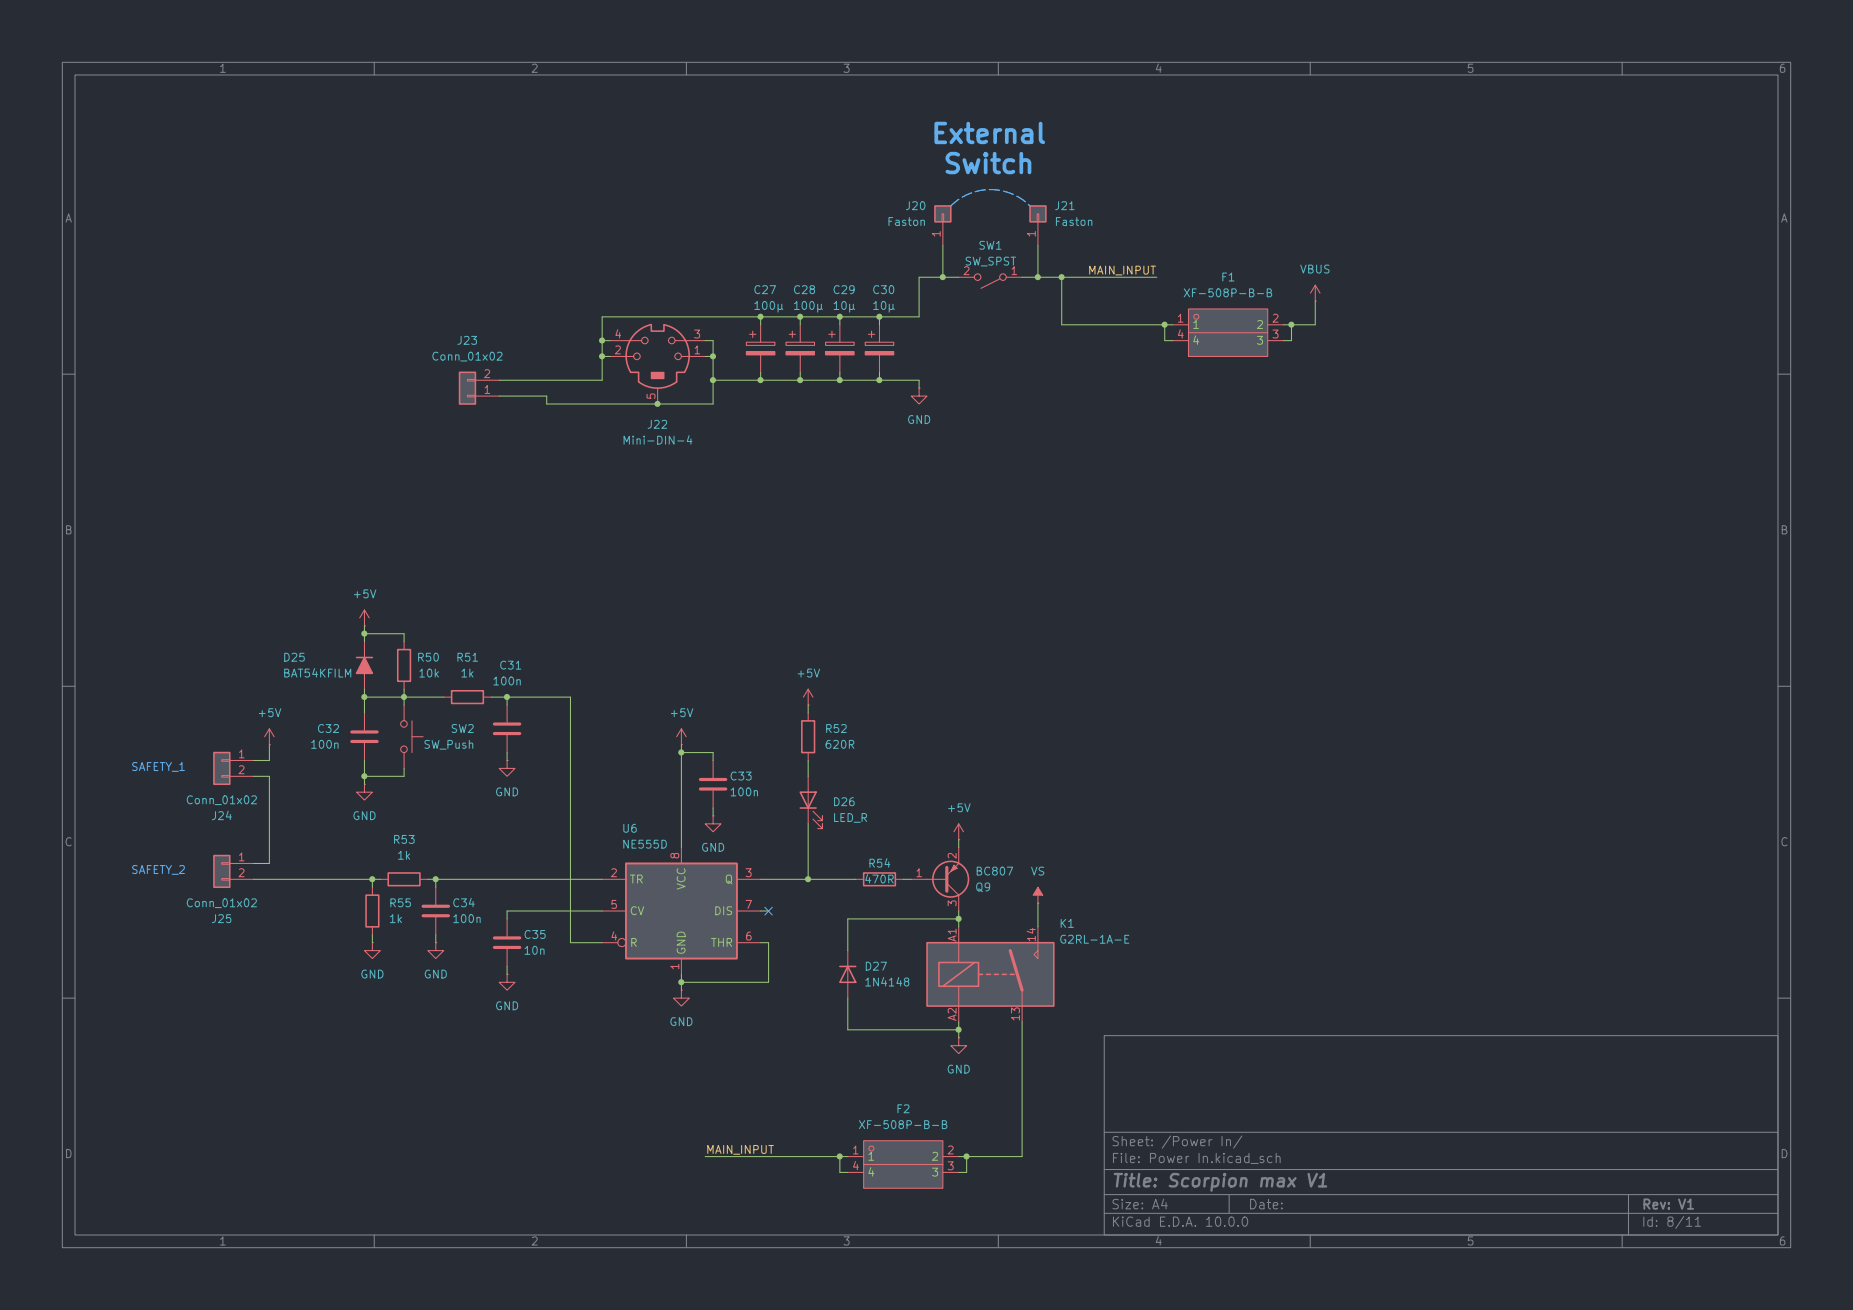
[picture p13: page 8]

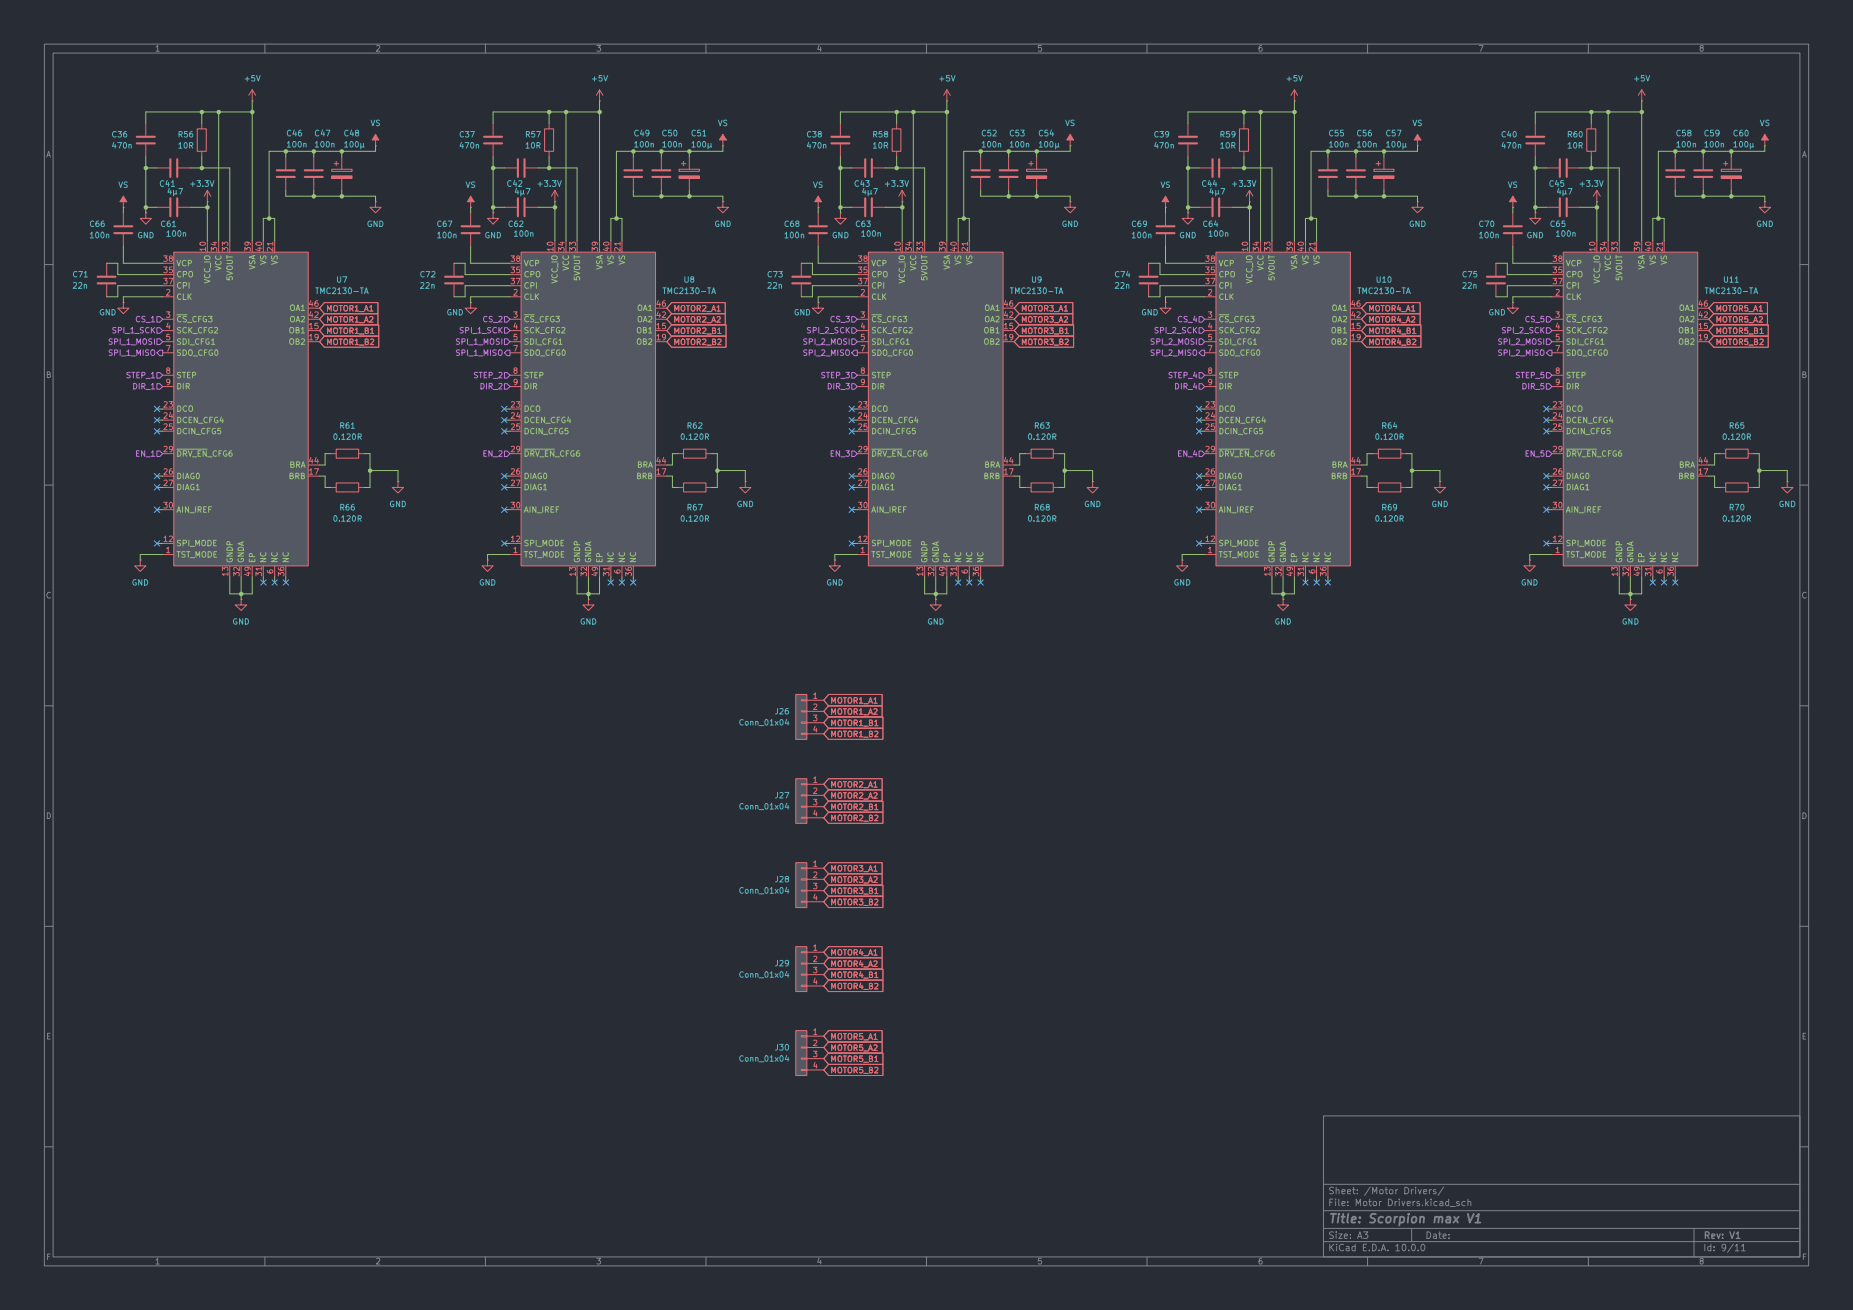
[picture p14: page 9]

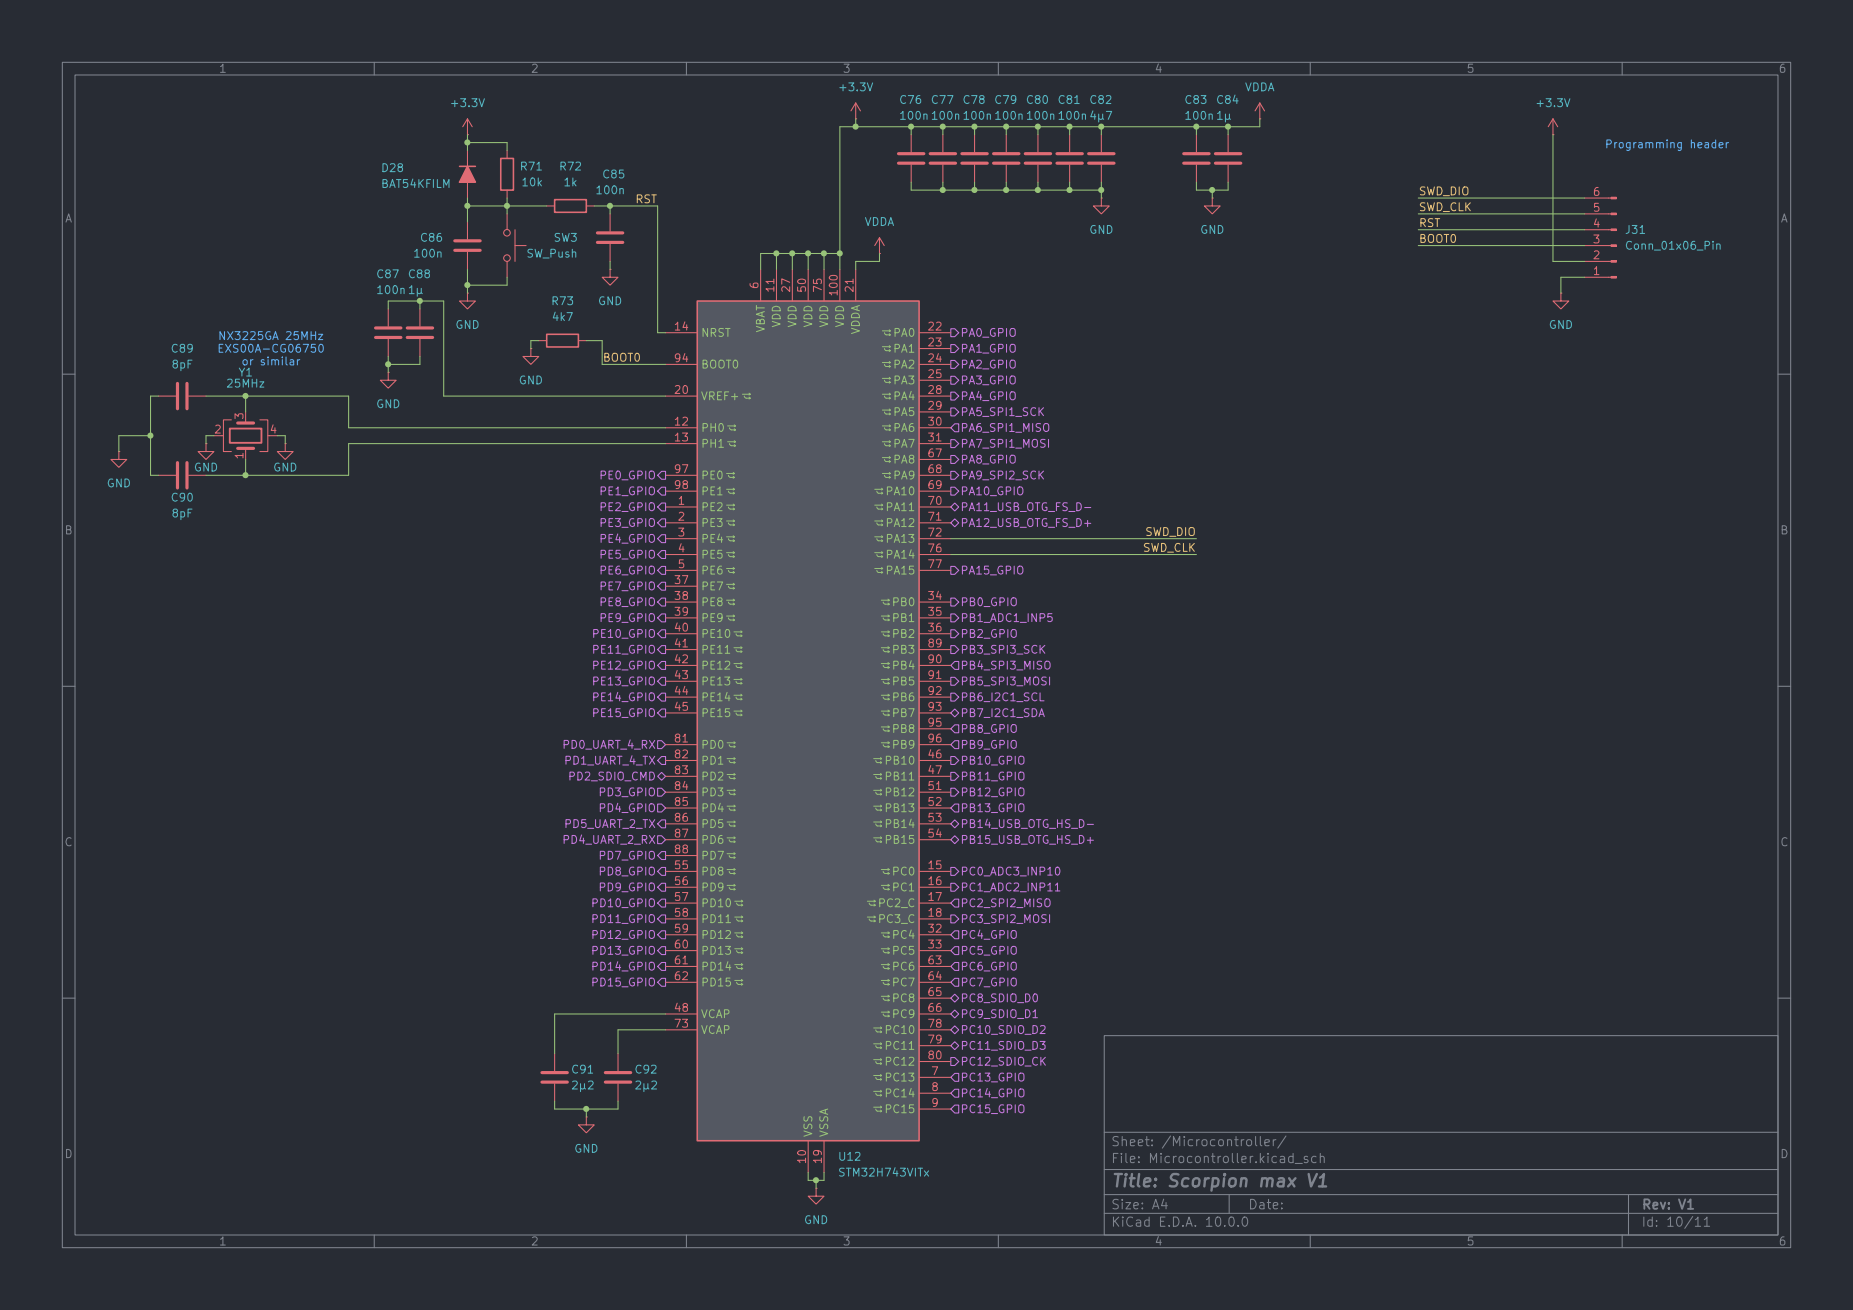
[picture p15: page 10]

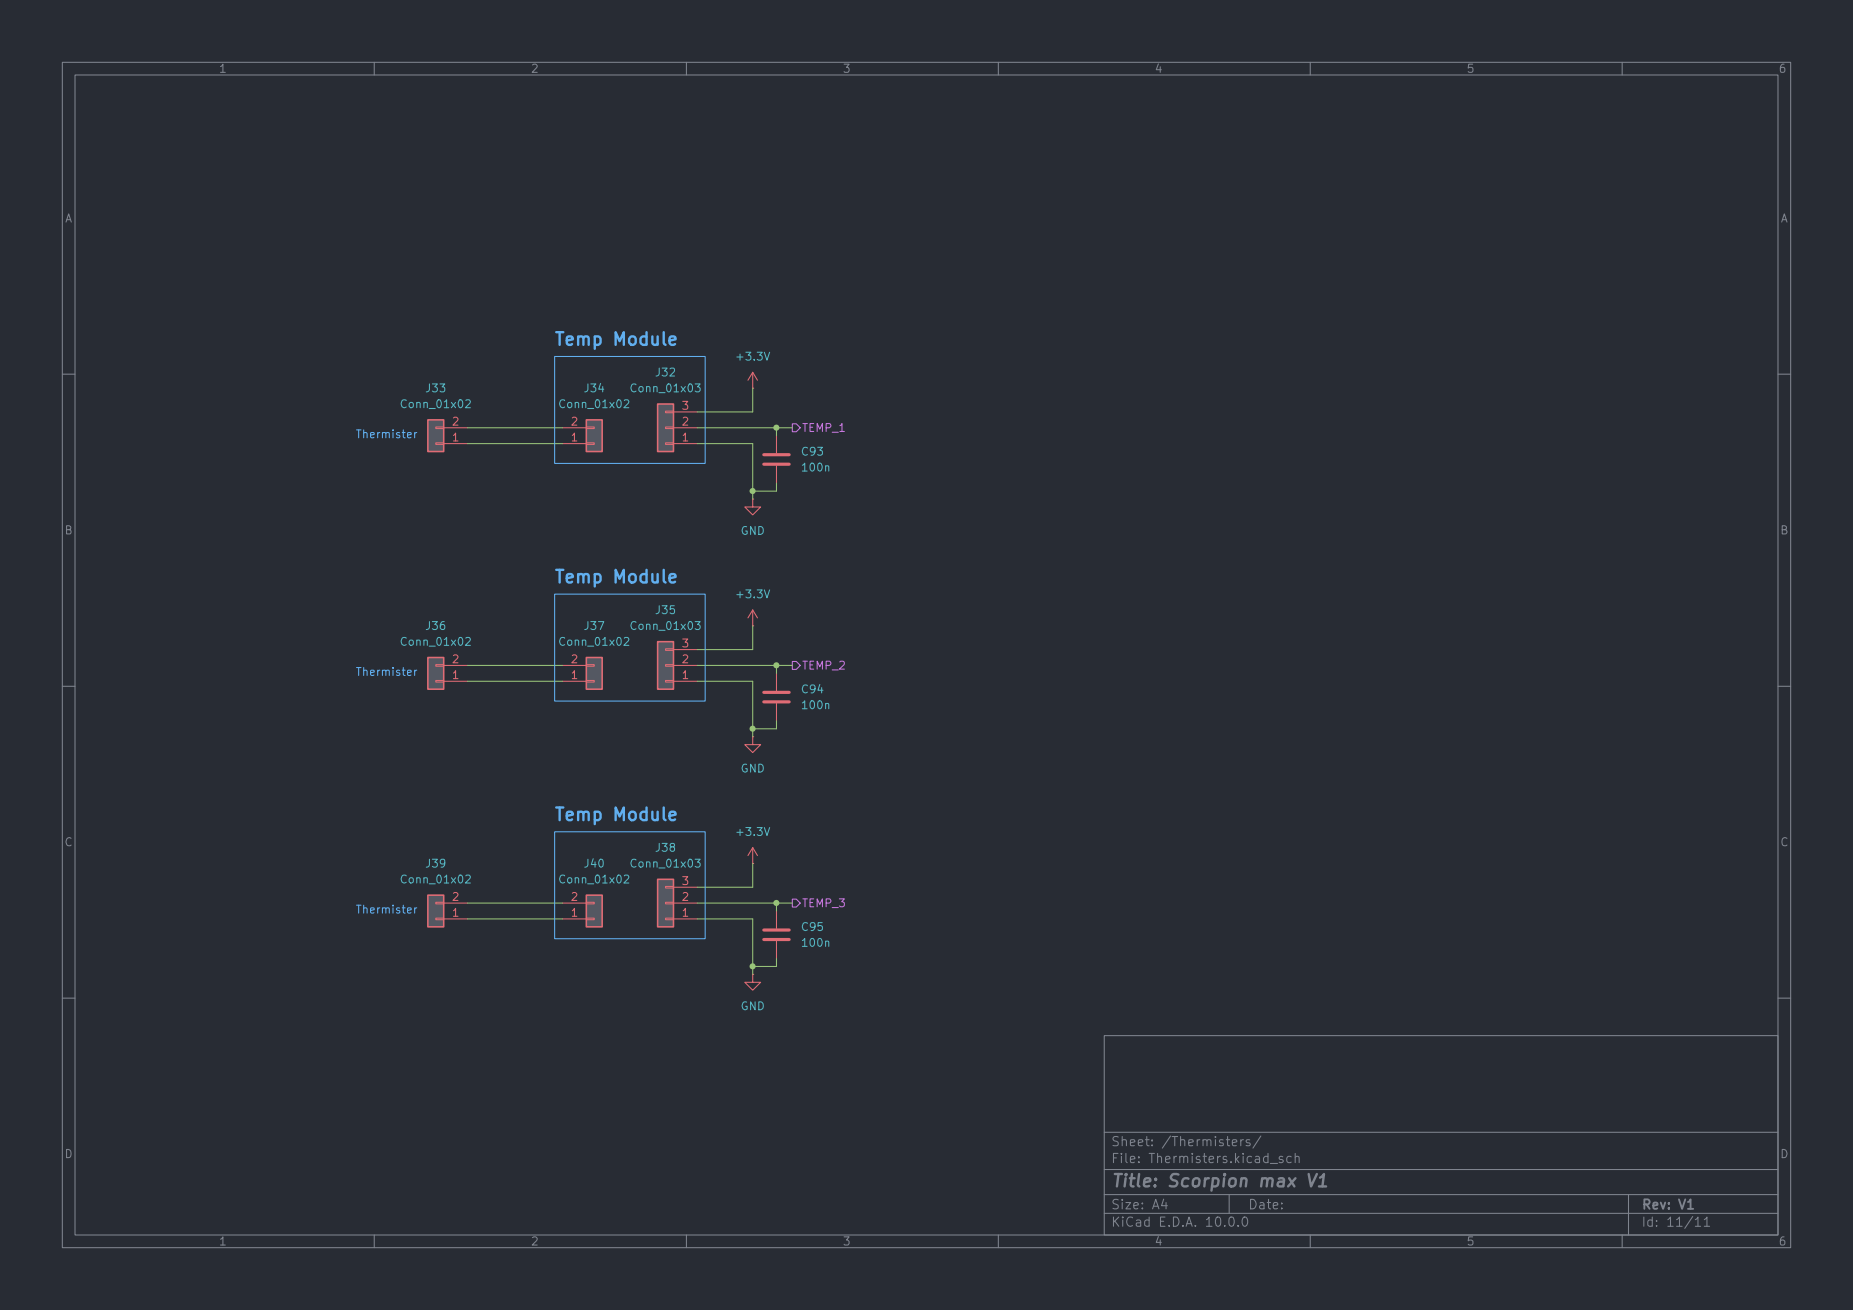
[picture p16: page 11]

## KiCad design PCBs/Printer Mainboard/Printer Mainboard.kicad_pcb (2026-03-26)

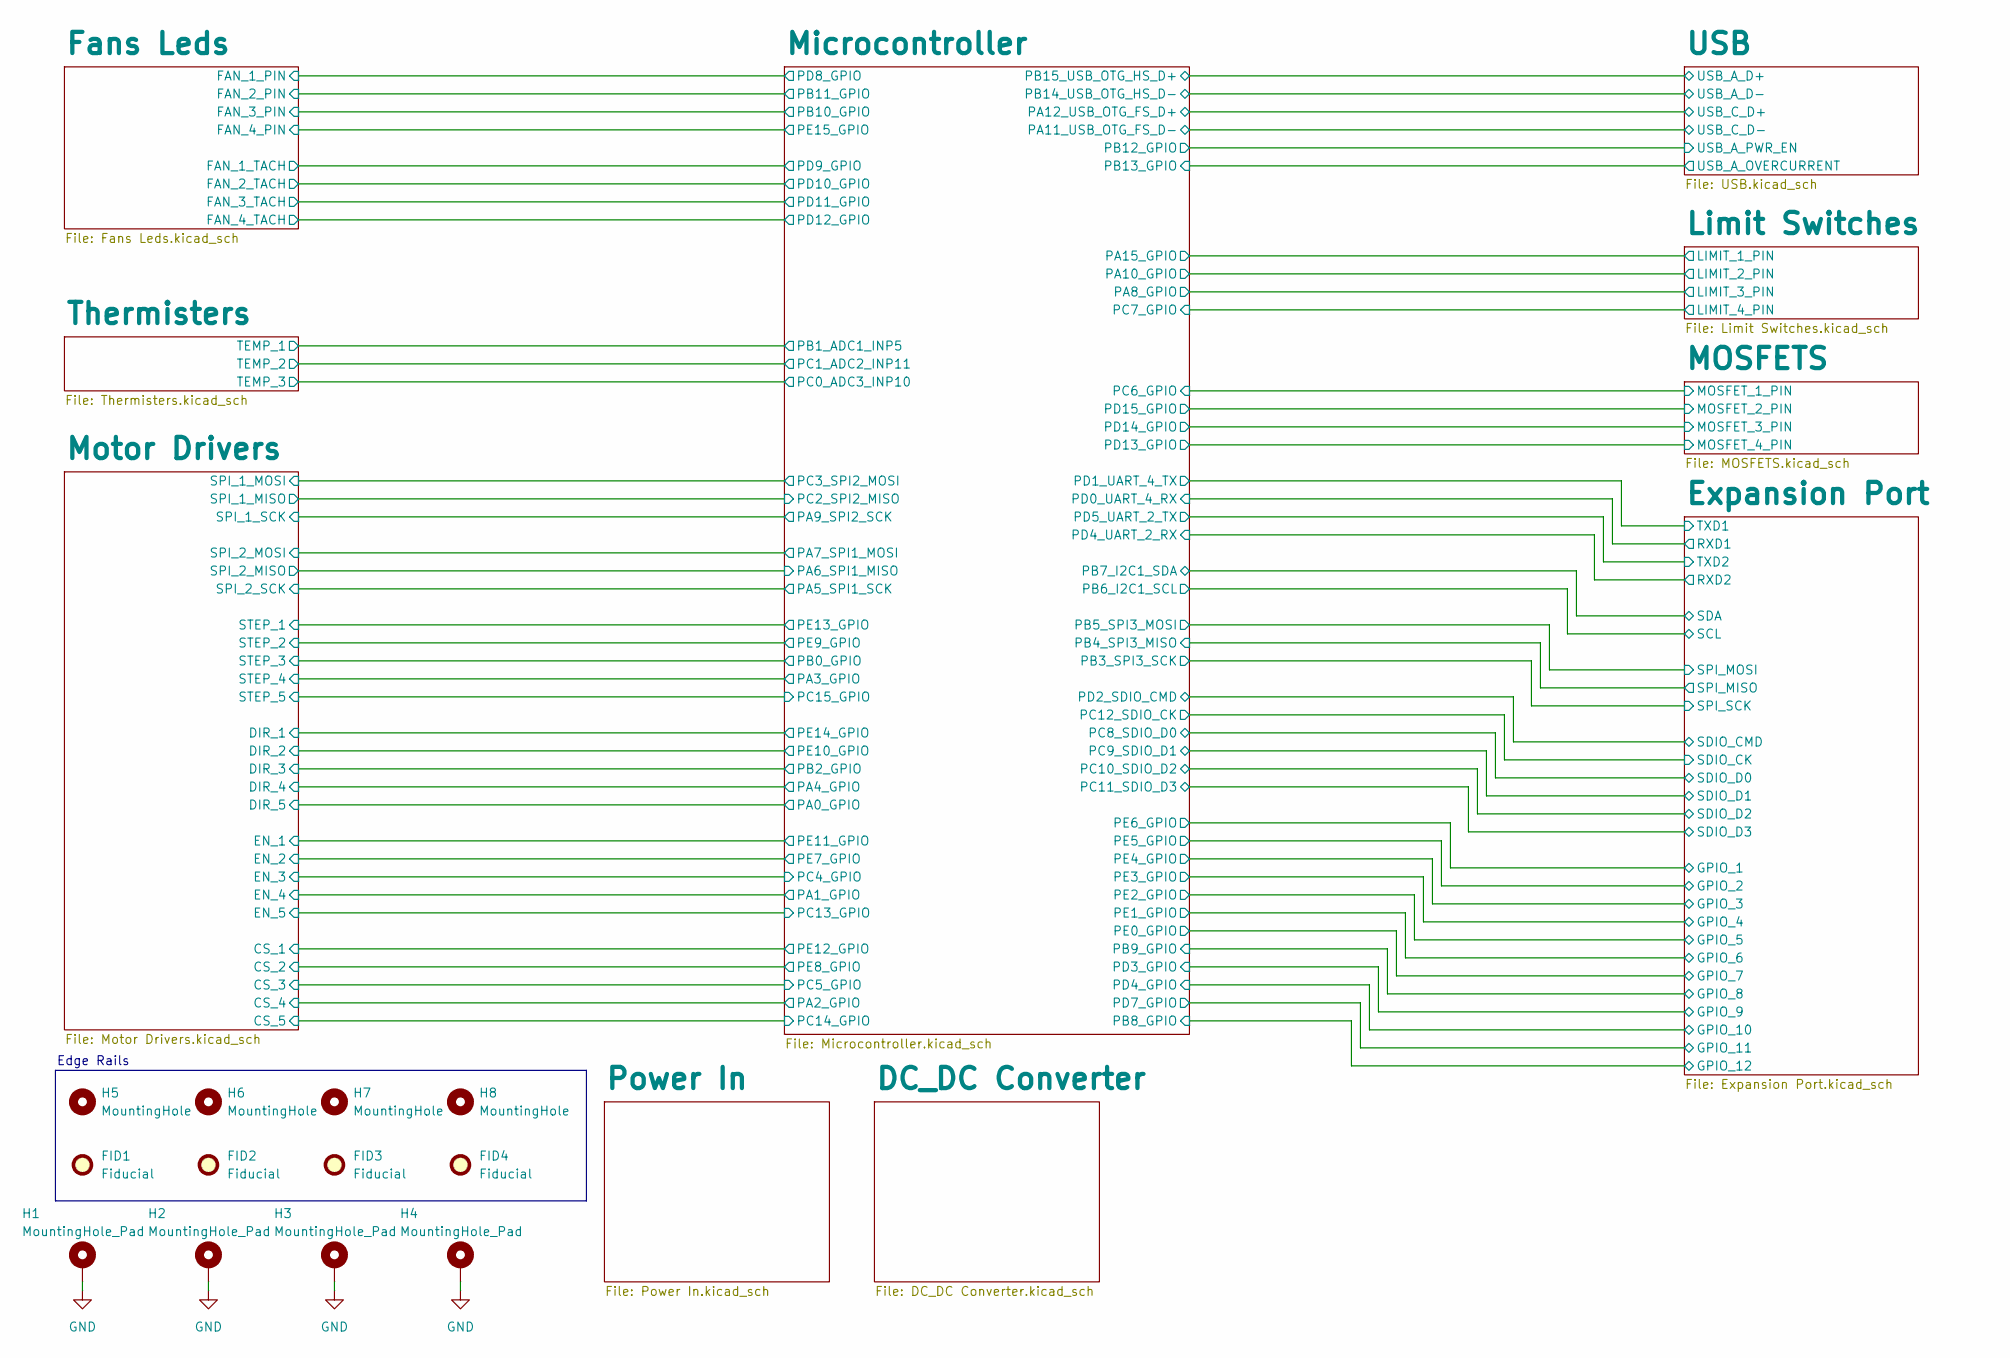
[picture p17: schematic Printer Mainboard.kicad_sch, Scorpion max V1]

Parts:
FID1, FID2, FID3, FID4: Fiducial; Fiducial_0.5mm_Mask1.5mm
H1, H2, H3, H4: MountingHole_Pad; MountingHole_3.2mm_M3_Pad
H5, H6, H7, H8: MountingHole; MountingHole_2mm

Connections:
GND: H1.1, H2.1, H3.1, H4.1; also elsewhere on the board

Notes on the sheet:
Edge Rails

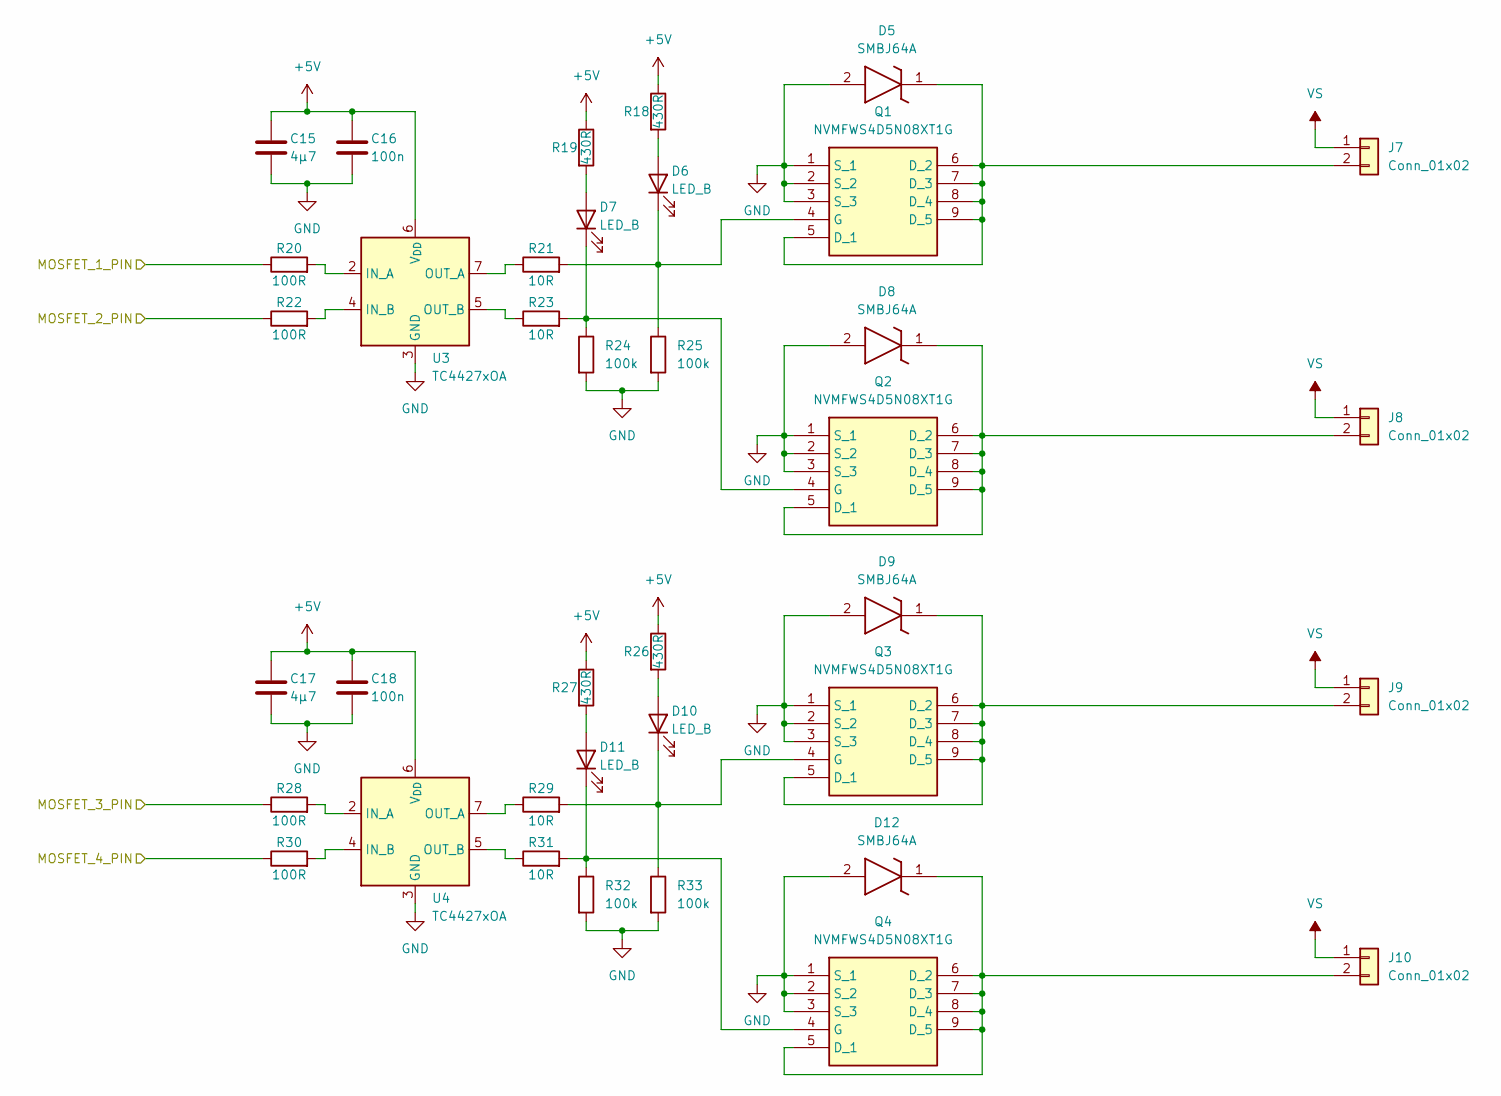
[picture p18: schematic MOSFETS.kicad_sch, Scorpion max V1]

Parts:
C15, C17: 4μ7; C_0805_2012Metric
C16, C18: 100n; C_0603_1608Metric
D5, D8, D9, D12: SMBJ64A; DIOM5436X250N; Manufacturer_Part_Number SMBJ64A
D6, D7, D10, D11: LED_B; LED_0603_1608Metric
J7, J8, J9, J10: Conn_01x02; CONN-TH_2P-P5.08_2EDG-5.08-2AW
Q1, Q2, Q3, Q4: NVMFWS4D5N08XT1G; NVMFS5C460NWFT1G; Mouser Part Number 863-NVMFWS4D5N08XT1G
R18, R19, R26, R27: 430R; R_0603_1608Metric
R20, R22, R28, R30: 100R; R_0603_1608Metric
R21, R23, R29, R31: 10R; R_0805_2012Metric
R24, R25, R32, R33: 100k; R_0603_1608Metric
U3, U4: TC4427xOA; SOIC-8_3.9x4.9mm_P1.27mm

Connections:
+5V: C15.1, C16.1, C17.1, C18.1, R18.1, R19.1, R26.1, R27.1, U3.6 (V_{DD}), U4.6 (V_{DD}); also elsewhere on the board
/MOSFETS/MOSFET_1_PIN: R20.1; also elsewhere on the board
/MOSFETS/MOSFET_2_PIN: R22.1; also elsewhere on the board
/MOSFETS/MOSFET_3_PIN: R28.1; also elsewhere on the board
/MOSFETS/MOSFET_4_PIN: R30.1; also elsewhere on the board
GND: C15.2, C16.2, C17.2, C18.2, D5.2 (A), D8.2 (A), D9.2 (A), D12.2 (A), Q1.1 (S_1), Q1.2 (S_2), Q1.3 (S_3), Q2.1 (S_1), Q2.2 (S_2), Q2.3 (S_3), Q3.1 (S_1), Q3.2 (S_2), Q3.3 (S_3), Q4.1 (S_1), Q4.2 (S_2), Q4.3 (S_3), R24.2, R25.2, R32.2, R33.2, U3.3 (GND), U4.3 (GND); also elsewhere on the board
unnamed: D5.1 (K), J7.2, Q1.5 (D_1), Q1.6 (D_2), Q1.7 (D_3), Q1.8 (D_4), Q1.9 (D_5)
unnamed: D6.2 (A), R18.2
unnamed: D6.1 (K), Q1.4 (G), R21.2, R25.1
unnamed: D7.2 (A), R19.2
unnamed: D7.1 (K), Q2.4 (G), R23.2, R24.1
unnamed: D8.1 (K), J8.2, Q2.5 (D_1), Q2.6 (D_2), Q2.7 (D_3), Q2.8 (D_4), Q2.9 (D_5)
unnamed: D9.1 (K), J9.2, Q3.5 (D_1), Q3.6 (D_2), Q3.7 (D_3), Q3.8 (D_4), Q3.9 (D_5)
unnamed: D10.2 (A), R26.2
unnamed: D10.1 (K), Q3.4 (G), R29.2, R33.1
unnamed: D11.2 (A), R27.2
unnamed: D11.1 (K), Q4.4 (G), R31.2, R32.1
unnamed: D12.1 (K), J10.2, Q4.5 (D_1), Q4.6 (D_2), Q4.7 (D_3), Q4.8 (D_4), Q4.9 (D_5)
unnamed: R20.2, U3.2 (IN_A)
unnamed: R22.2, U3.4 (IN_B)
unnamed: R21.1, U3.7 (OUT_A)
unnamed: R23.1, U3.5 (OUT_B)
unnamed: R28.2, U4.2 (IN_A)
unnamed: R30.2, U4.4 (IN_B)
unnamed: R29.1, U4.7 (OUT_A)
unnamed: R31.1, U4.5 (OUT_B)
VS: J7.1, J8.1, J9.1, J10.1; also elsewhere on the board

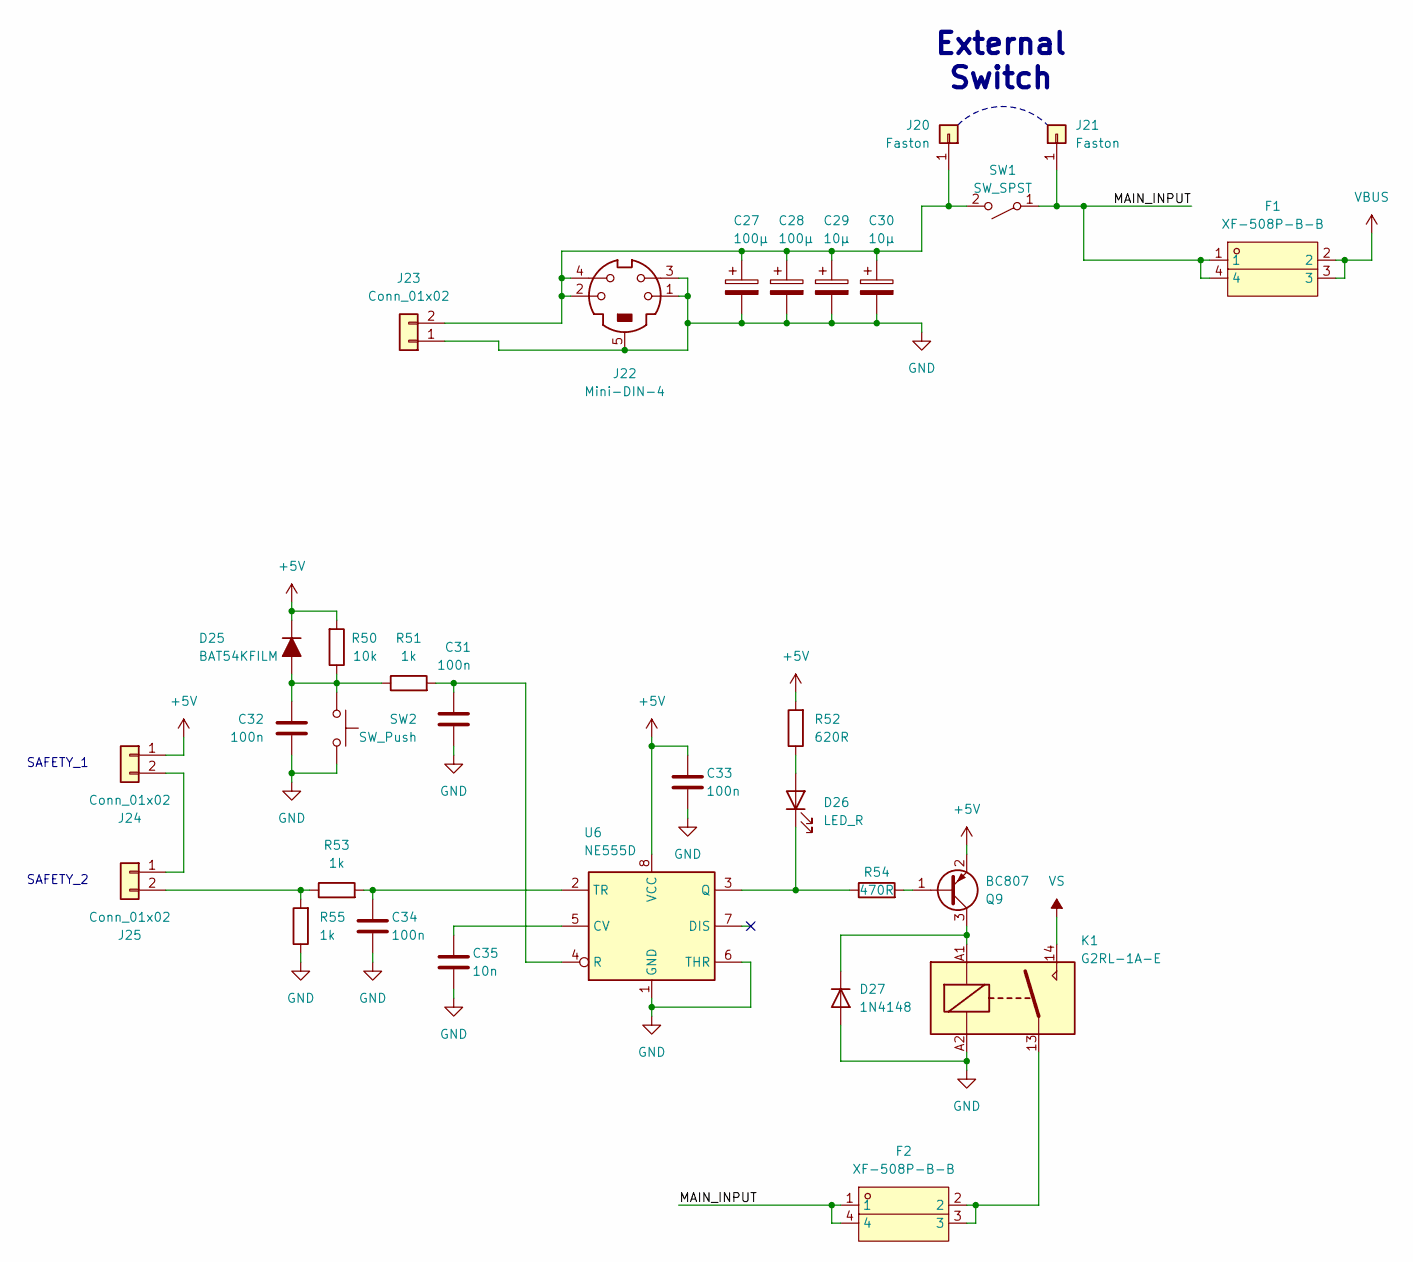
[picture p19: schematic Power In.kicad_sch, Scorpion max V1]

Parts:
C27, C28: 100μ; CP_Elec_10x10
C29, C30: 10μ; CP_Elec_6.3x5.8
C31, C32, C33, C34: 100n; C_0603_1608Metric
C35: 10n; C_0603_1608Metric
D25: BAT54KFILM; D_SOD-523
D26: LED_R; LED_0603_1608Metric
D27: 1N4148; D_SOD-523
F1, F2: XF-508P-B-B; FUSE-TH_4P-L16.0-W6.7; LCSC Part C19727305
J20, J21: Faston; CONN-TH_63849-1
J22: Mini-DIN-4; CONN-TH_DIN-422
J23: Conn_01x02; CONN-TH_MKDS3-2-5.08
J24, J25: Conn_01x02; PinHeader_1x02_P2.54mm_Vertical
K1: G2RL-1A-E; Relay_SPST_Omron_G2RL-1A-E
Q9: BC807; SOT-23
R50: 10k; R_0603_1608Metric
R51, R53, R55: 1k; R_0603_1608Metric
R52: 620R; R_0603_1608Metric
R54: 470R; R_0603_1608Metric
SW1: SW_SPST; SW-TH_SDDJF31100
SW2: SW_Push; B3F3120
U6: NE555D; SOIC-8_3.9x4.9mm_P1.27mm

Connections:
+5V: C33.1, D25.1 (K), J24.1, Q9.2 (E), R50.2, R52.2, U6.8 (VCC); also elsewhere on the board
/Power In/MAIN_INPUT: F1.1, F1.4, F2.1, F2.4, J21.1, SW1.1 (A)
GND: C27.2, C28.2, C29.2, C30.2, C31.2, C32.2, C33.2, C34.2, C35.2, D27.2 (A), J22.1, J22.3, J22.5, J23.1, K1.A2, R55.1, SW2.1, U6.1 (GND), U6.6 (THR); also elsewhere on the board
unnamed: C32.1, D25.2 (A), R50.1, R51.1, SW2.2
unnamed: D26.2 (A), R52.1
unnamed: D26.1 (K), R54.1, U6.3 (Q)
unnamed: D27.1 (K), K1.A1, Q9.3 (C)
unnamed: F2.2, F2.3, K1.13
unnamed: C27.1, C28.1, C29.1, C30.1, J20.1, J22.2, J22.4, J23.2, SW1.2 (B)
unnamed: J24.2, J25.1
unnamed: J25.2, R53.1, R55.2
unnamed: Q9.1 (B), R54.2
unnamed: C35.1, U6.5 (CV)
unnamed: C31.1, R51.2, U6.4 (R)
unnamed: C34.1, R53.2, U6.2 (TR)
VBUS: F1.2, F1.3; also elsewhere on the board
VS: K1.14; also elsewhere on the board

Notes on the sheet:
SAFETY_1
External Switch
SAFETY_2

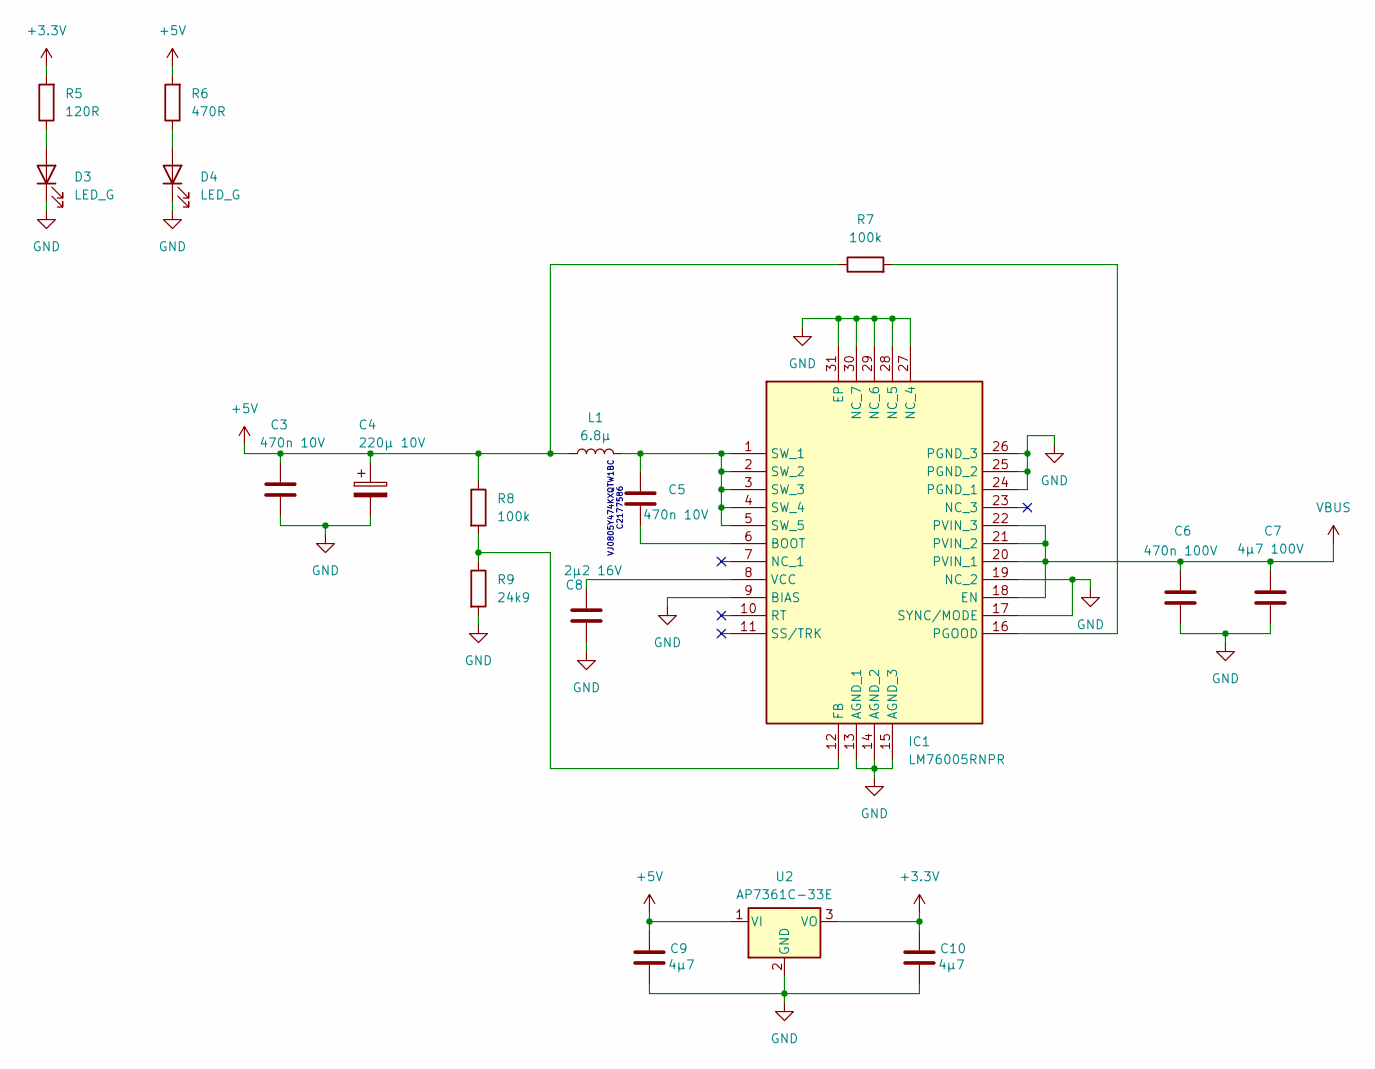
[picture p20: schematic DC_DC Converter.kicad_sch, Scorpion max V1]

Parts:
C3, C5: 470n 10V; C_0805_2012Metric
C4: 220μ 10V; CP_EIA-7343-43_Kemet-X
C6: 470n 100V; C_1210_3225Metric
C7: 4μ7 100V; C_1210_3225Metric
C8: 2μ2 16V; C_0603_1608Metric
C9, C10: 4μ7; C_0805_2012Metric
D3, D4: LED_G; LED_0603_1608Metric
IC1: LM76005RNPR; QFN50P400X600X80-31N-D; Mouser Part Number 595-LM76005RNPR
L1: 6.8μ; L_Vishay_IHLP-4040
R5: 120R; R_0603_1608Metric
R6: 470R; R_0603_1608Metric
R7, R8: 100k; R_0603_1608Metric
R9: 24k9; R_0603_1608Metric
U2: AP7361C-33E; SOT-223-3_TabPin2

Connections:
+3.3V: C10.1, R5.2, U2.3 (VO); also elsewhere on the board
+5V: C3.1, C4.1, C9.1, L1.1, R6.2, R7.1, R8.1, U2.1 (VI); also elsewhere on the board
GND: C3.2, C4.2, C6.2, C7.2, C8.2, C9.2, C10.2, D3.1 (K), D4.1 (K), IC1.9 (BIAS), IC1.13 (AGND_1), IC1.14 (AGND_2), IC1.15 (AGND_3), IC1.17 (SYNC/MODE), IC1.19 (NC_2), IC1.24 (PGND_1), IC1.25 (PGND_2), IC1.26 (PGND_3), IC1.27 (NC_4), IC1.28 (NC_5), IC1.29 (NC_6), IC1.30 (NC_7), IC1.31 (EP), R9.2, U2.2 (GND); also elsewhere on the board
unnamed: D3.2 (A), R5.1
unnamed: D4.2 (A), R6.1
unnamed: C5.1, IC1.6 (BOOT)
unnamed: IC1.12 (FB), R8.2, R9.1
unnamed: IC1.16 (PGOOD), R7.2
unnamed: C5.2, IC1.1 (SW_1), IC1.2 (SW_2), IC1.3 (SW_3), IC1.4 (SW_4), IC1.5 (SW_5), L1.2
unnamed: C8.1, IC1.8 (VCC)
VBUS: C6.1, C7.1, IC1.18 (EN), IC1.20 (PVIN_1), IC1.21 (PVIN_2), IC1.22 (PVIN_3); also elsewhere on the board

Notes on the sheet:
VJ0805Y474KXQTW1BC C2177586

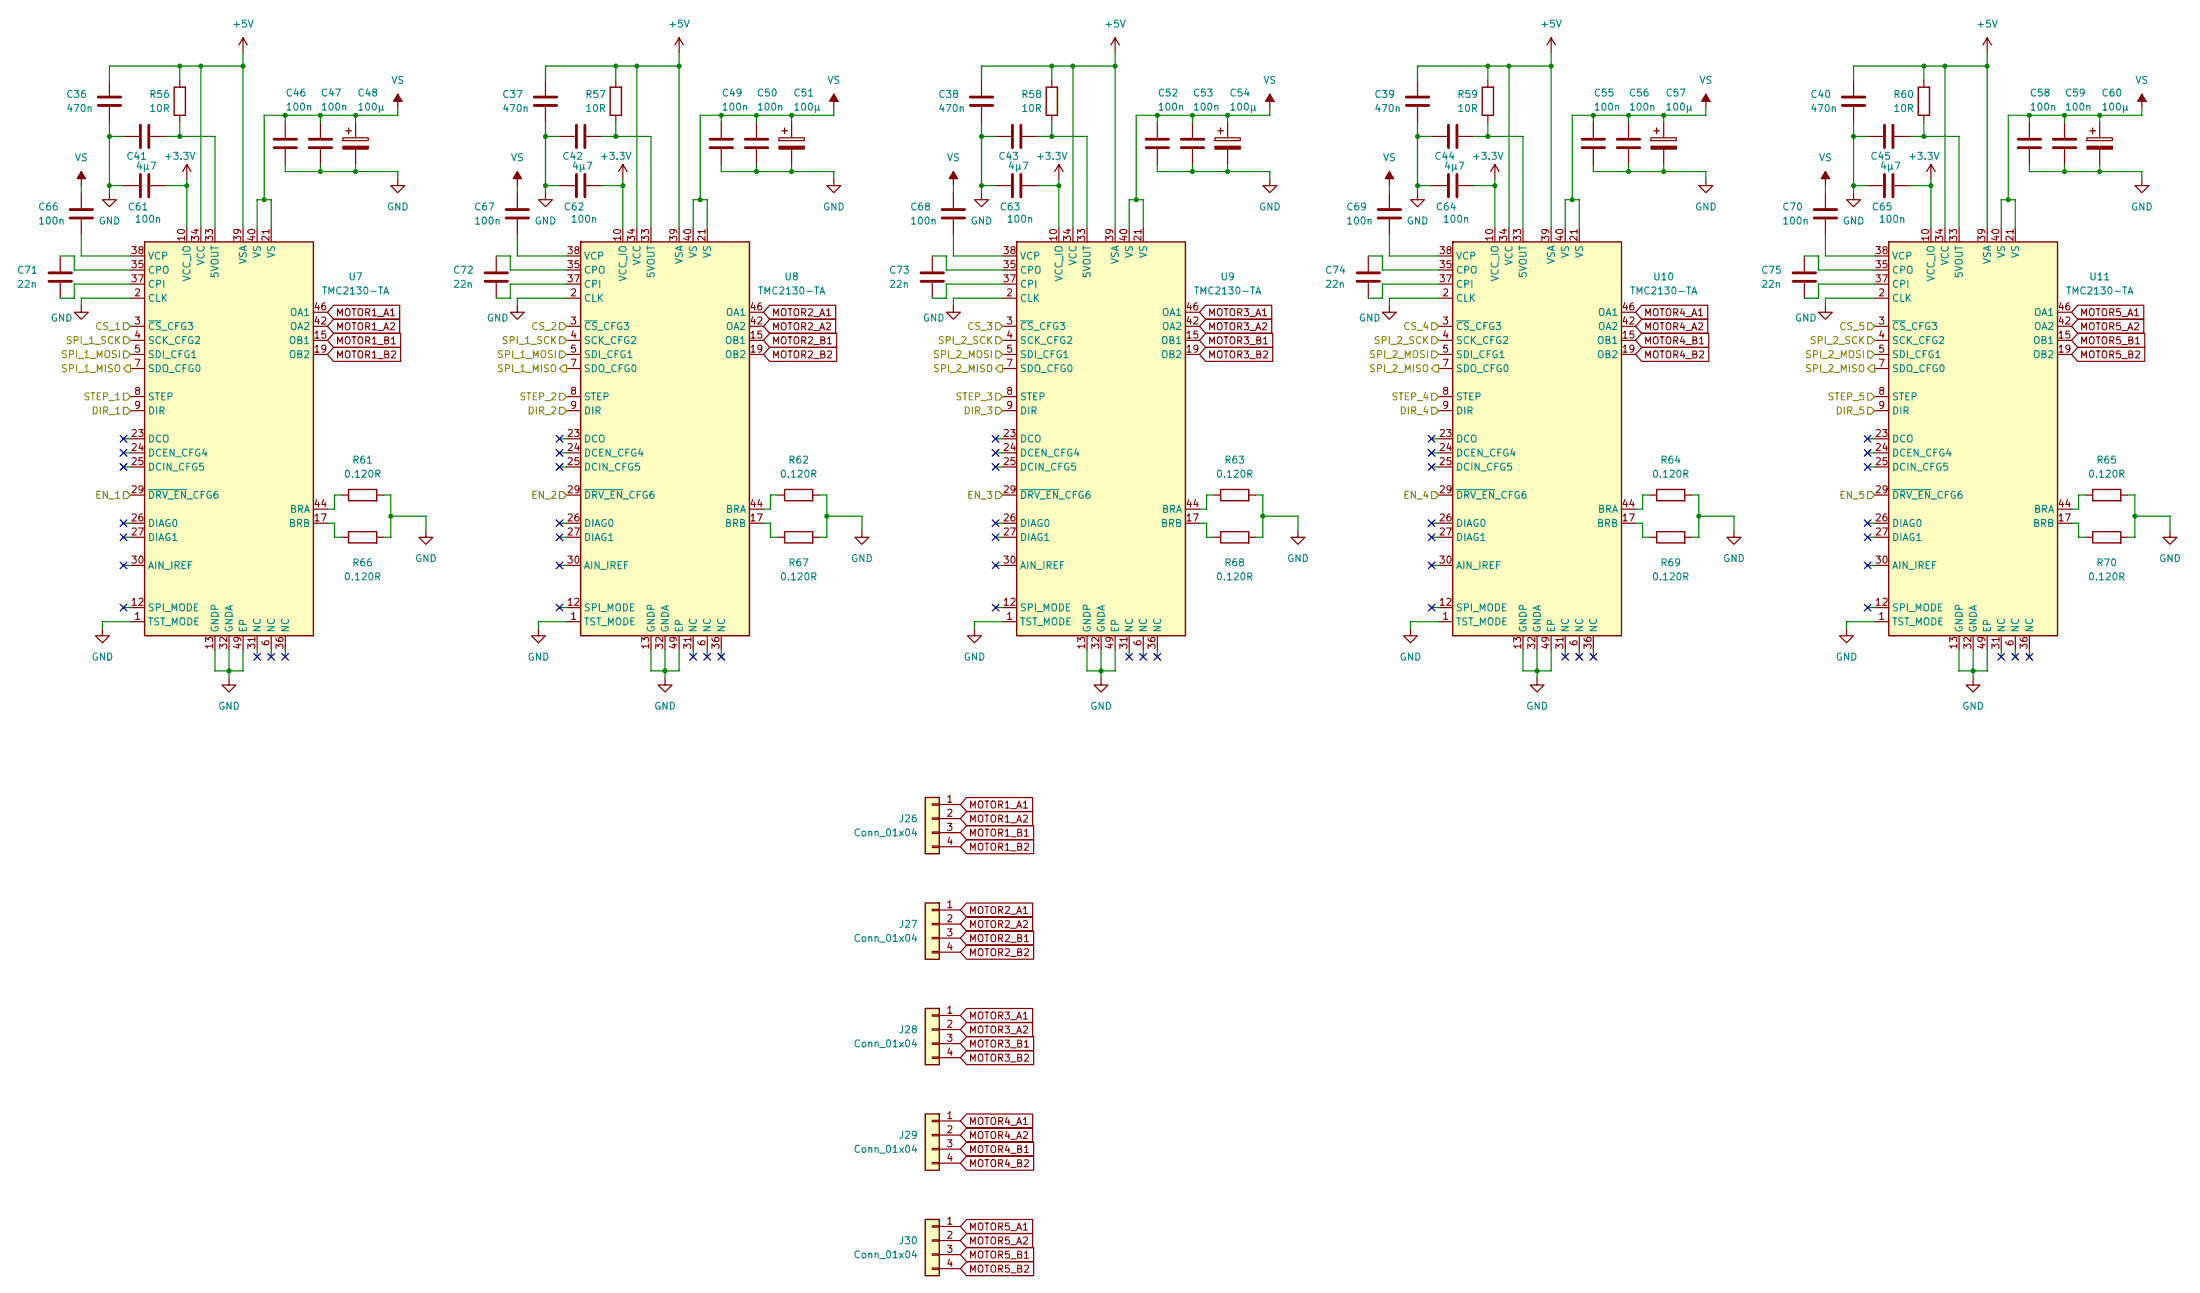
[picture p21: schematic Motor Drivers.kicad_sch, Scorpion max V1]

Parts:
C36, C37, C38, C39, C40: 470n; C_0603_1608Metric
C41, C42, C43, C44, C45: 4μ7; C_0805_2012Metric
C46, C47, C49, C50, C52, C53, C55, C56, C58, C59, C61, C62, C63, C64, C65, C66, C67, C68, C69, C70: 100n; C_0603_1608Metric
C48, C51, C54, C57, C60: 100μ; CP_Elec_10x10
C71, C72, C73, C74, C75: 22n; C_0603_1608Metric
J26, J27, J28, J29, J30: Conn_01x04; JST_XH_B4B-XH-A_1x04_P2.50mm_Vertical
R56, R57, R58, R59, R60: 10R; R_0603_1608Metric
R61, R62, R63, R64, R65, R66, R67, R68, R69, R70: 0.120R; R_1206_3216Metric
U7, U8, U9, U10, U11: TMC2130-TA; TQFP-48-1EP_7x7mm_P0.5mm_EP5x5mm_ThermalVias

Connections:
+3.3V: C61.1, C62.1, C63.1, C64.1, C65.1, U7.10 (VCC_IO), U8.10 (VCC_IO), U9.10 (VCC_IO), U10.10 (VCC_IO), U11.10 (VCC_IO); also elsewhere on the board
+5V: C36.2, C37.2, C38.2, C39.2, C40.2, R56.2, R57.2, R58.2, R59.2, R60.2, U7.34 (VCC), U7.39 (VSA), U8.34 (VCC), U8.39 (VSA), U9.34 (VCC), U9.39 (VSA), U10.34 (VCC), U10.39 (VSA), U11.34 (VCC), U11.39 (VSA); also elsewhere on the board
/Microcontroller/PA0_GPIO: U11.9 (DIR); also elsewhere on the board
/Microcontroller/PA1_GPIO: U10.29 (~DRV_EN_CFG6); also elsewhere on the board
/Microcontroller/PA2_GPIO: U10.3 (~CS_CFG3); also elsewhere on the board
/Microcontroller/PA3_GPIO: U10.8 (STEP); also elsewhere on the board
/Microcontroller/PA4_GPIO: U10.9 (DIR); also elsewhere on the board
/Microcontroller/PA5_SPI1_SCK: U9.4 (SCK_CFG2), U10.4 (SCK_CFG2), U11.4 (SCK_CFG2); also elsewhere on the board
/Microcontroller/PA6_SPI1_MISO: U9.7 (SDO_CFG0), U10.7 (SDO_CFG0), U11.7 (SDO_CFG0); also elsewhere on the board
/Microcontroller/PA7_SPI1_MOSI: U9.5 (SDI_CFG1), U10.5 (SDI_CFG1), U11.5 (SDI_CFG1); also elsewhere on the board
/Microcontroller/PA9_SPI2_SCK: U7.4 (SCK_CFG2), U8.4 (SCK_CFG2); also elsewhere on the board
/Microcontroller/PB0_GPIO: U9.8 (STEP); also elsewhere on the board
/Microcontroller/PB2_GPIO: U9.9 (DIR); also elsewhere on the board
/Microcontroller/PC2_SPI2_MISO: U7.7 (SDO_CFG0), U8.7 (SDO_CFG0); also elsewhere on the board
/Microcontroller/PC3_SPI2_MOSI: U7.5 (SDI_CFG1), U8.5 (SDI_CFG1); also elsewhere on the board
/Microcontroller/PC4_GPIO: U9.29 (~DRV_EN_CFG6); also elsewhere on the board
/Microcontroller/PC5_GPIO: U9.3 (~CS_CFG3); also elsewhere on the board
/Microcontroller/PC13_GPIO: U11.29 (~DRV_EN_CFG6); also elsewhere on the board
/Microcontroller/PC14_GPIO: U11.3 (~CS_CFG3); also elsewhere on the board
/Microcontroller/PC15_GPIO: U11.8 (STEP); also elsewhere on the board
/Microcontroller/PE7_GPIO: U8.29 (~DRV_EN_CFG6); also elsewhere on the board
/Microcontroller/PE8_GPIO: U8.3 (~CS_CFG3); also elsewhere on the board
/Microcontroller/PE9_GPIO: U8.8 (STEP); also elsewhere on the board
/Microcontroller/PE10_GPIO: U8.9 (DIR); also elsewhere on the board
/Microcontroller/PE11_GPIO: U7.29 (~DRV_EN_CFG6); also elsewhere on the board
/Microcontroller/PE12_GPIO: U7.3 (~CS_CFG3); also elsewhere on the board
/Microcontroller/PE13_GPIO: U7.8 (STEP); also elsewhere on the board
/Microcontroller/PE14_GPIO: U7.9 (DIR); also elsewhere on the board
GND: C36.1, C37.1, C38.1, C39.1, C40.1, C41.2, C42.2, C43.2, C44.2, C45.2, C46.1, C47.1, C48.2, C49.1, C50.1, C51.2, C52.1, C53.1, C54.2, C55.1, C56.1, C57.2, C58.1, C59.1, C60.2, C61.2, C62.2, C63.2, C64.2, C65.2, R61.2, R62.2, R63.2, R64.2, R65.2, R66.2, R67.2, R68.2, R69.2, R70.2, U7.1 (TST_MODE), U7.2 (CLK), U7.13 (GNDP), U7.32 (GNDA), U7.48 (GNDP), U7.49 (EP), U8.1 (TST_MODE), U8.2 (CLK), U8.13 (GNDP), U8.32 (GNDA), U8.48 (GNDP), U8.49 (EP), U9.1 (TST_MODE), U9.2 (CLK), U9.13 (GNDP), U9.32 (GNDA), U9.48 (GNDP), U9.49 (EP), U10.1 (TST_MODE), U10.2 (CLK), U10.13 (GNDP), U10.32 (GNDA), U10.48 (GNDP), U10.49 (EP), U11.1 (TST_MODE), U11.2 (CLK), U11.13 (GNDP), U11.32 (GNDA), U11.48 (GNDP), U11.49 (EP); also elsewhere on the board
MOTOR1_A1: J26.1, U7.46 (OA1)
MOTOR1_A2: J26.2, U7.42 (OA2)
MOTOR1_B1: J26.3, U7.15 (OB1)
MOTOR1_B2: J26.4, U7.19 (OB2)
MOTOR2_A1: J27.1, U8.46 (OA1)
MOTOR2_A2: J27.2, U8.42 (OA2)
MOTOR2_B1: J27.3, U8.15 (OB1)
MOTOR2_B2: J27.4, U8.19 (OB2)
MOTOR3_A1: J28.1, U9.46 (OA1)
MOTOR3_A2: J28.2, U9.42 (OA2)
MOTOR3_B1: J28.3, U9.15 (OB1)
MOTOR3_B2: J28.4, U9.19 (OB2)
MOTOR4_A1: J29.1, U10.46 (OA1)
MOTOR4_A2: J29.2, U10.42 (OA2)
MOTOR4_B1: J29.3, U10.15 (OB1)
MOTOR4_B2: J29.4, U10.19 (OB2)
MOTOR5_A1: J30.1, U11.46 (OA1)
MOTOR5_A2: J30.2, U11.42 (OA2)
MOTOR5_B1: J30.3, U11.15 (OB1)
MOTOR5_B2: J30.4, U11.19 (OB2)
unnamed: C41.1, R56.1, U7.33 (5VOUT)
unnamed: R61.1, U7.44 (BRA)
unnamed: R66.1, U7.17 (BRB)
unnamed: C71.1, U7.37 (CPI)
unnamed: C71.2, U7.35 (CPO)
unnamed: C66.1, U7.38 (VCP)
unnamed: C42.1, R57.1, U8.33 (5VOUT)
unnamed: R62.1, U8.44 (BRA)
unnamed: R67.1, U8.17 (BRB)
unnamed: C72.1, U8.37 (CPI)
unnamed: C72.2, U8.35 (CPO)
unnamed: C67.1, U8.38 (VCP)
unnamed: C43.1, R58.1, U9.33 (5VOUT)
unnamed: R63.1, U9.44 (BRA)
unnamed: R68.1, U9.17 (BRB)
unnamed: C73.1, U9.37 (CPI)
unnamed: C73.2, U9.35 (CPO)
unnamed: C68.1, U9.38 (VCP)
unnamed: C44.1, R59.1, U10.33 (5VOUT)
unnamed: R64.1, U10.44 (BRA)
unnamed: R69.1, U10.17 (BRB)
unnamed: C74.1, U10.37 (CPI)
unnamed: C74.2, U10.35 (CPO)
unnamed: C69.1, U10.38 (VCP)
unnamed: C45.1, R60.1, U11.33 (5VOUT)
unnamed: R65.1, U11.44 (BRA)
unnamed: R70.1, U11.17 (BRB)
unnamed: C75.1, U11.37 (CPI)
unnamed: C75.2, U11.35 (CPO)
unnamed: C70.1, U11.38 (VCP)
VS: C46.2, C47.2, C48.1, C49.2, C50.2, C51.1, C52.2, C53.2, C54.1, C55.2, C56.2, C57.1, C58.2, C59.2, C60.1, C66.2, C67.2, C68.2, C69.2, C70.2, U7.21 (VS), U7.40 (VS), U8.21 (VS), U8.40 (VS), U9.21 (VS), U9.40 (VS), U10.21 (VS), U10.40 (VS), U11.21 (VS), U11.40 (VS); also elsewhere on the board

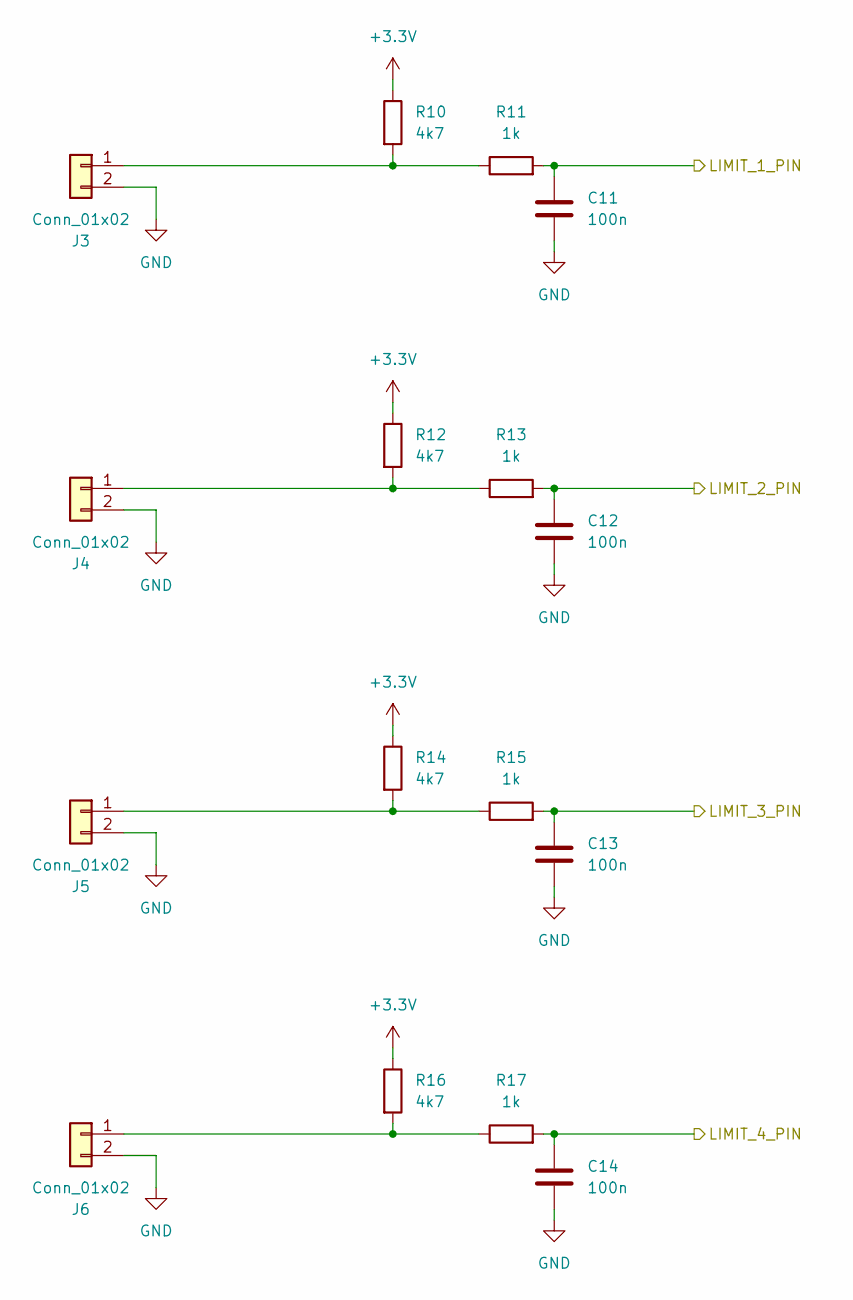
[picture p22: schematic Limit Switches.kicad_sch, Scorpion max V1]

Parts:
C11, C12, C13, C14: 100n; C_0603_1608Metric
J3, J4, J5, J6: Conn_01x02; JST_XH_B2B-XH-A_1x02_P2.50mm_Vertical
R10, R12, R14, R16: 4k7; R_0603_1608Metric
R11, R13, R15, R17: 1k; R_0603_1608Metric

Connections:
+3.3V: R10.1, R12.1, R14.1, R16.1; also elsewhere on the board
/Limit Switches/LIMIT_1_PIN: C11.1, R11.2; also elsewhere on the board
/Limit Switches/LIMIT_2_PIN: C12.1, R13.2; also elsewhere on the board
/Limit Switches/LIMIT_3_PIN: C13.1, R15.2; also elsewhere on the board
/Limit Switches/LIMIT_4_PIN: C14.1, R17.2; also elsewhere on the board
GND: C11.2, C12.2, C13.2, C14.2, J3.2, J4.2, J5.2, J6.2; also elsewhere on the board
unnamed: J3.1, R10.2, R11.1
unnamed: J4.1, R12.2, R13.1
unnamed: J5.1, R14.2, R15.1
unnamed: J6.1, R16.2, R17.1

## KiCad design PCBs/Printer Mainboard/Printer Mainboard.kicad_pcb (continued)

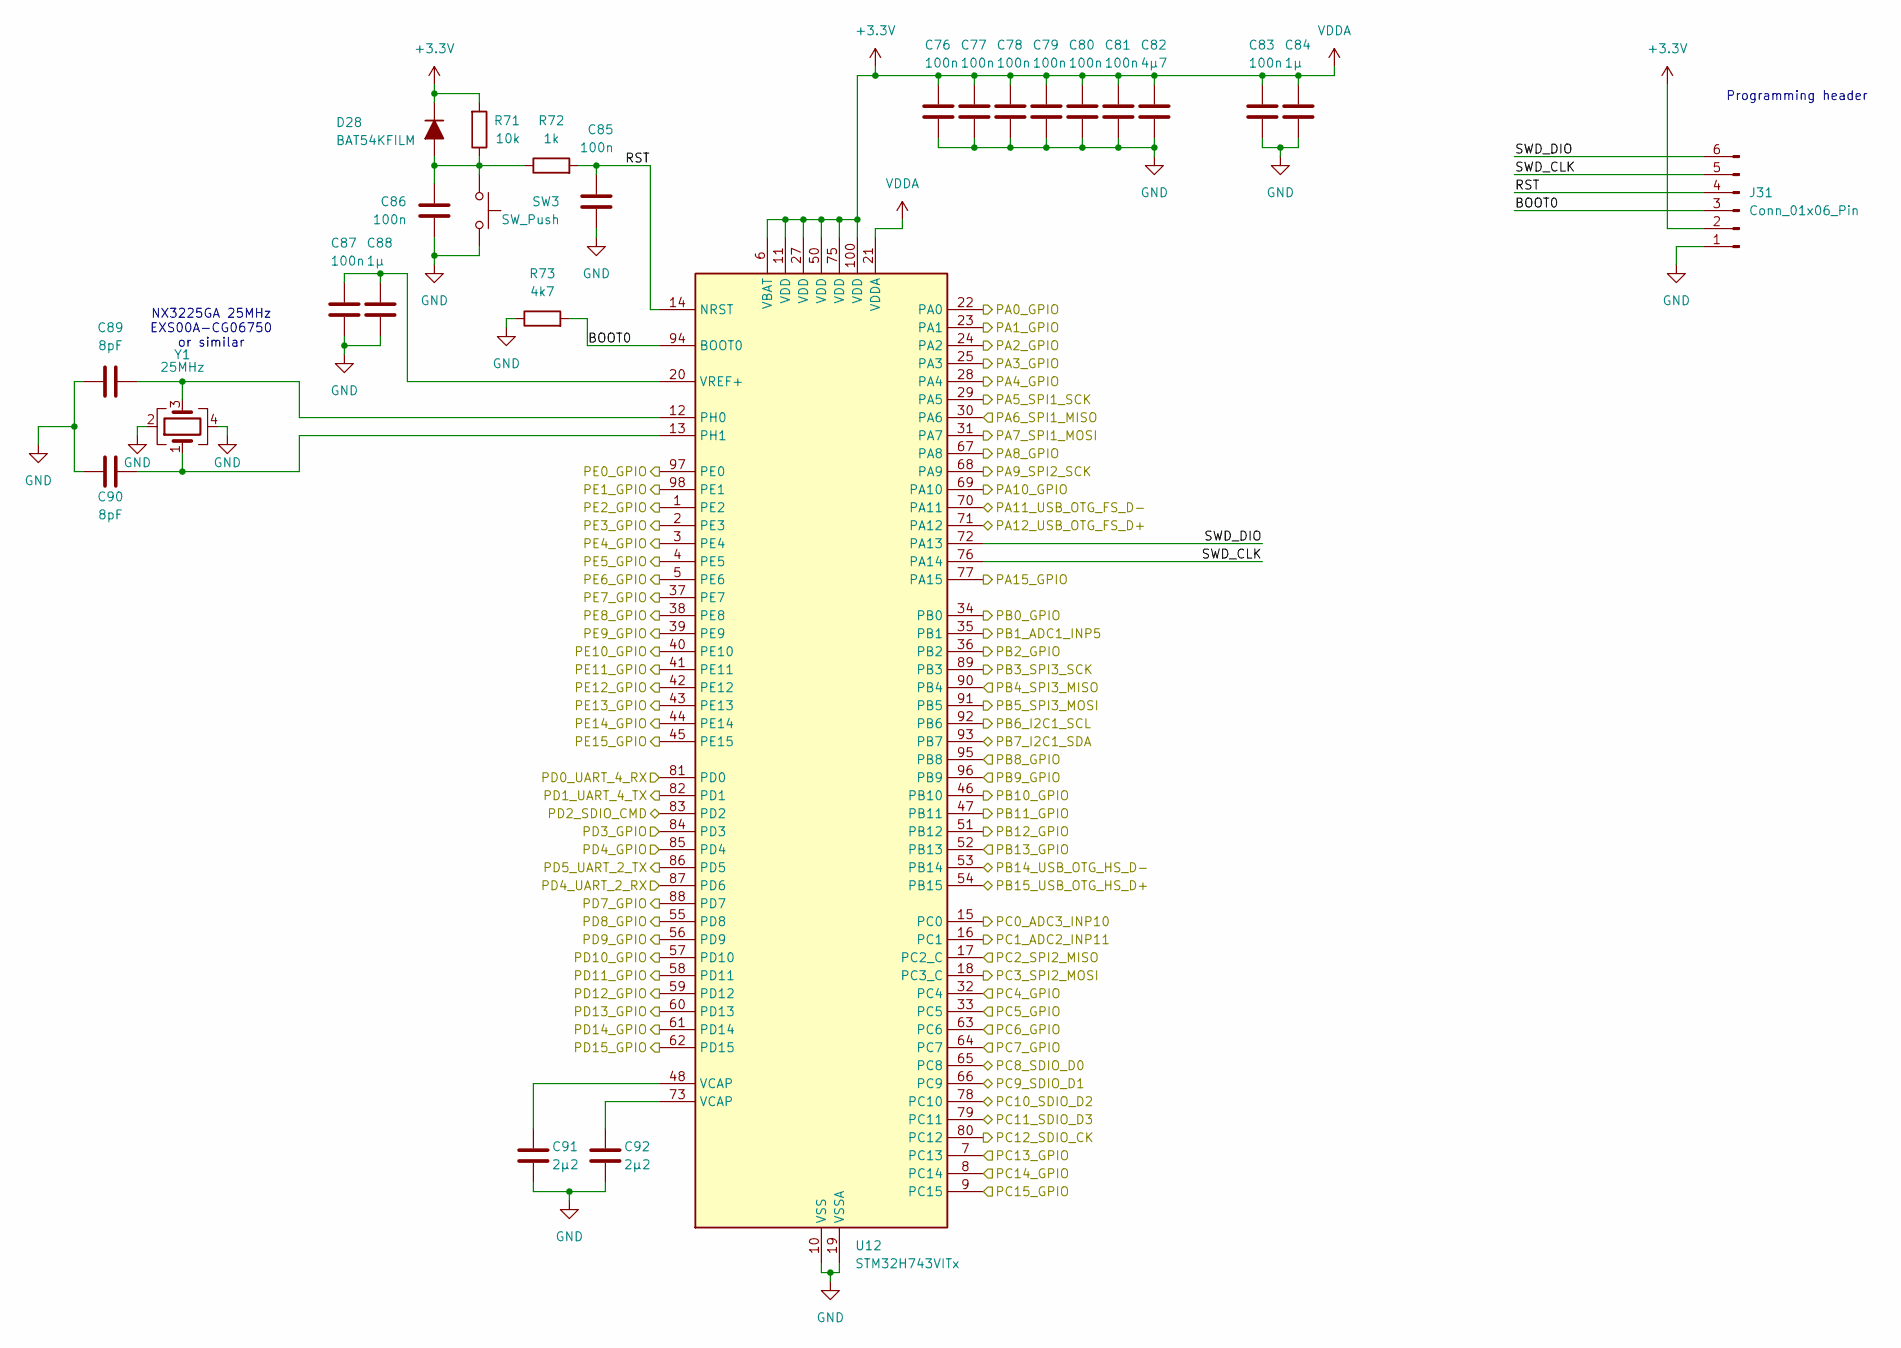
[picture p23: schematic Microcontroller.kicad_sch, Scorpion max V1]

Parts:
C76, C77, C78, C79, C80, C81, C83, C85, C86, C87: 100n; C_0603_1608Metric
C82: 4μ7; C_0805_2012Metric
C84, C88: 1μ; C_0603_1608Metric
C89, C90: 8pF; C_0603_1608Metric
C91, C92: 2μ2; C_0603_1608Metric
D28: BAT54KFILM; D_SOD-523
J31: Conn_01x06_Pin; PinHeader_1x06_P2.54mm_Vertical
R71: 10k; R_0603_1608Metric
R72: 1k; R_0603_1608Metric
R73: 4k7; R_0603_1608Metric
SW3: SW_Push; B3F3120
U12: STM32H743VITx; LQFP-100_14x14mm_P0.5mm
Y1: 25MHz; Crystal_SMD_3225-4Pin_3.2x2.5mm

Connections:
+3.3V: C76.1, C77.1, C78.1, C79.1, C80.1, C81.1, C82.1, C83.1, C84.1, D28.1 (K), J31.2, R71.2, U12.6 (VBAT), U12.11 (VDD), U12.21 (VDDA), U12.27 (VDD), U12.50 (VDD), U12.75 (VDD), U12.100 (VDD); also elsewhere on the board
/Expansion Port/GPIO_1: U12.5 (PE6); also elsewhere on the board
/Expansion Port/GPIO_2: U12.4 (PE5); also elsewhere on the board
/Expansion Port/GPIO_3: U12.3 (PE4); also elsewhere on the board
/Expansion Port/GPIO_4: U12.2 (PE3); also elsewhere on the board
/Expansion Port/GPIO_5: U12.1 (PE2); also elsewhere on the board
/Expansion Port/GPIO_6: U12.98 (PE1); also elsewhere on the board
/Expansion Port/GPIO_7: U12.97 (PE0); also elsewhere on the board
/Expansion Port/GPIO_8: U12.96 (PB9); also elsewhere on the board
/Expansion Port/GPIO_9: U12.84 (PD3); also elsewhere on the board
/Expansion Port/GPIO_10: U12.85 (PD4); also elsewhere on the board
/Expansion Port/GPIO_11: U12.88 (PD7); also elsewhere on the board
/Expansion Port/GPIO_12: U12.95 (PB8); also elsewhere on the board
/Expansion Port/RXD1: U12.81 (PD0); also elsewhere on the board
/Expansion Port/RXD2: U12.87 (PD6); also elsewhere on the board
/Expansion Port/SCL: U12.92 (PB6); also elsewhere on the board
/Expansion Port/SDA: U12.93 (PB7); also elsewhere on the board
/Expansion Port/SDIO_CK: U12.80 (PC12); also elsewhere on the board
/Expansion Port/SDIO_CMD: U12.83 (PD2); also elsewhere on the board
/Expansion Port/SDIO_D0: U12.65 (PC8); also elsewhere on the board
/Expansion Port/SDIO_D1: U12.66 (PC9); also elsewhere on the board
/Expansion Port/SDIO_D2: U12.78 (PC10); also elsewhere on the board
/Expansion Port/SDIO_D3: U12.79 (PC11); also elsewhere on the board
/Expansion Port/SPI_MISO: U12.90 (PB4); also elsewhere on the board
/Expansion Port/SPI_MOSI: U12.91 (PB5); also elsewhere on the board
/Expansion Port/SPI_SCK: U12.89 (PB3); also elsewhere on the board
/Expansion Port/TXD1: U12.82 (PD1); also elsewhere on the board
/Expansion Port/TXD2: U12.86 (PD5); also elsewhere on the board
/Fans Leds/FAN_1_PIN: U12.55 (PD8); also elsewhere on the board
/Fans Leds/FAN_1_TACH: U12.56 (PD9); also elsewhere on the board
/Fans Leds/FAN_2_PIN: U12.47 (PB11); also elsewhere on the board
/Fans Leds/FAN_2_TACH: U12.57 (PD10); also elsewhere on the board
/Fans Leds/FAN_3_PIN: U12.46 (PB10); also elsewhere on the board
/Fans Leds/FAN_3_TACH: U12.58 (PD11); also elsewhere on the board
/Fans Leds/FAN_4_PIN: U12.45 (PE15); also elsewhere on the board
/Fans Leds/FAN_4_TACH: U12.59 (PD12); also elsewhere on the board
/Limit Switches/LIMIT_1_PIN: U12.77 (PA15); also elsewhere on the board
/Limit Switches/LIMIT_2_PIN: U12.69 (PA10); also elsewhere on the board
/Limit Switches/LIMIT_3_PIN: U12.67 (PA8); also elsewhere on the board
/Limit Switches/LIMIT_4_PIN: U12.64 (PC7); also elsewhere on the board
/MOSFETS/MOSFET_1_PIN: U12.63 (PC6); also elsewhere on the board
/MOSFETS/MOSFET_2_PIN: U12.62 (PD15); also elsewhere on the board
/MOSFETS/MOSFET_3_PIN: U12.61 (PD14); also elsewhere on the board
/MOSFETS/MOSFET_4_PIN: U12.60 (PD13); also elsewhere on the board
/Microcontroller/BOOT0: J31.3, R73.2, U12.94 (BOOT0)
/Microcontroller/PA0_GPIO: U12.22 (PA0); also elsewhere on the board
/Microcontroller/PA1_GPIO: U12.23 (PA1); also elsewhere on the board
/Microcontroller/PA2_GPIO: U12.24 (PA2); also elsewhere on the board
/Microcontroller/PA3_GPIO: U12.25 (PA3); also elsewhere on the board
/Microcontroller/PA4_GPIO: U12.28 (PA4); also elsewhere on the board
/Microcontroller/PA5_SPI1_SCK: U12.29 (PA5); also elsewhere on the board
/Microcontroller/PA6_SPI1_MISO: U12.30 (PA6); also elsewhere on the board
/Microcontroller/PA7_SPI1_MOSI: U12.31 (PA7); also elsewhere on the board
/Microcontroller/PA9_SPI2_SCK: U12.68 (PA9); also elsewhere on the board
/Microcontroller/PB0_GPIO: U12.34 (PB0); also elsewhere on the board
/Microcontroller/PB1_ADC1_INP5: U12.35 (PB1); also elsewhere on the board
/Microcontroller/PB2_GPIO: U12.36 (PB2); also elsewhere on the board
/Microcontroller/PB12_GPIO: U12.51 (PB12); also elsewhere on the board
/Microcontroller/PB13_GPIO: U12.52 (PB13); also elsewhere on the board
/Microcontroller/PC0_ADC3_INP10: U12.15 (PC0); also elsewhere on the board
/Microcontroller/PC1_ADC2_INP11: U12.16 (PC1); also elsewhere on the board
/Microcontroller/PC2_SPI2_MISO: U12.17 (PC2_C); also elsewhere on the board
/Microcontroller/PC3_SPI2_MOSI: U12.18 (PC3_C); also elsewhere on the board
/Microcontroller/PC4_GPIO: U12.32 (PC4); also elsewhere on the board
/Microcontroller/PC5_GPIO: U12.33 (PC5); also elsewhere on the board
/Microcontroller/PC13_GPIO: U12.7 (PC13); also elsewhere on the board
/Microcontroller/PC14_GPIO: U12.8 (PC14); also elsewhere on the board
/Microcontroller/PC15_GPIO: U12.9 (PC15); also elsewhere on the board
/Microcontroller/PE7_GPIO: U12.37 (PE7); also elsewhere on the board
/Microcontroller/PE8_GPIO: U12.38 (PE8); also elsewhere on the board
/Microcontroller/PE9_GPIO: U12.39 (PE9); also elsewhere on the board
/Microcontroller/PE10_GPIO: U12.40 (PE10); also elsewhere on the board
/Microcontroller/PE11_GPIO: U12.41 (PE11); also elsewhere on the board
/Microcontroller/PE12_GPIO: U12.42 (PE12); also elsewhere on the board
/Microcontroller/PE13_GPIO: U12.43 (PE13); also elsewhere on the board
/Microcontroller/PE14_GPIO: U12.44 (PE14); also elsewhere on the board
/Microcontroller/RST: C85.1, J31.4, R72.2, U12.14 (NRST)
/Microcontroller/SWD_CLK: J31.5, U12.76 (PA14)
/Microcontroller/SWD_DIO: J31.6, U12.72 (PA13)
/USB/USB_A_D+: U12.54 (PB15); also elsewhere on the board
/USB/USB_A_D-: U12.53 (PB14); also elsewhere on the board
/USB/USB_C_D+: U12.71 (PA12); also elsewhere on the board
/USB/USB_C_D-: U12.70 (PA11); also elsewhere on the board
GND: C76.2, C77.2, C78.2, C79.2, C80.2, C81.2, C82.2, C83.2, C84.2, C85.2, C86.2, C87.2, C88.2, C89.1, C90.1, C91.2, C92.2, J31.1, R73.1, SW3.1, U12.10 (VSS), U12.19 (VSSA), U12.26 (VSS), U12.49 (VSS), U12.74 (VSS), U12.99 (VSS), Y1.2, Y1.4; also elsewhere on the board
unnamed: C91.1, U12.48 (VCAP)
unnamed: C92.1, U12.73 (VCAP)
unnamed: C86.1, D28.2 (A), R71.1, R72.1, SW3.2
unnamed: C89.2, U12.12 (PH0), Y1.3
unnamed: C90.2, U12.13 (PH1), Y1.1
unnamed: C87.1, C88.1, U12.20 (VREF+)

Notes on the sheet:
Programming header
NX3225GA 25MHz EXS00A-CG06750 or similar

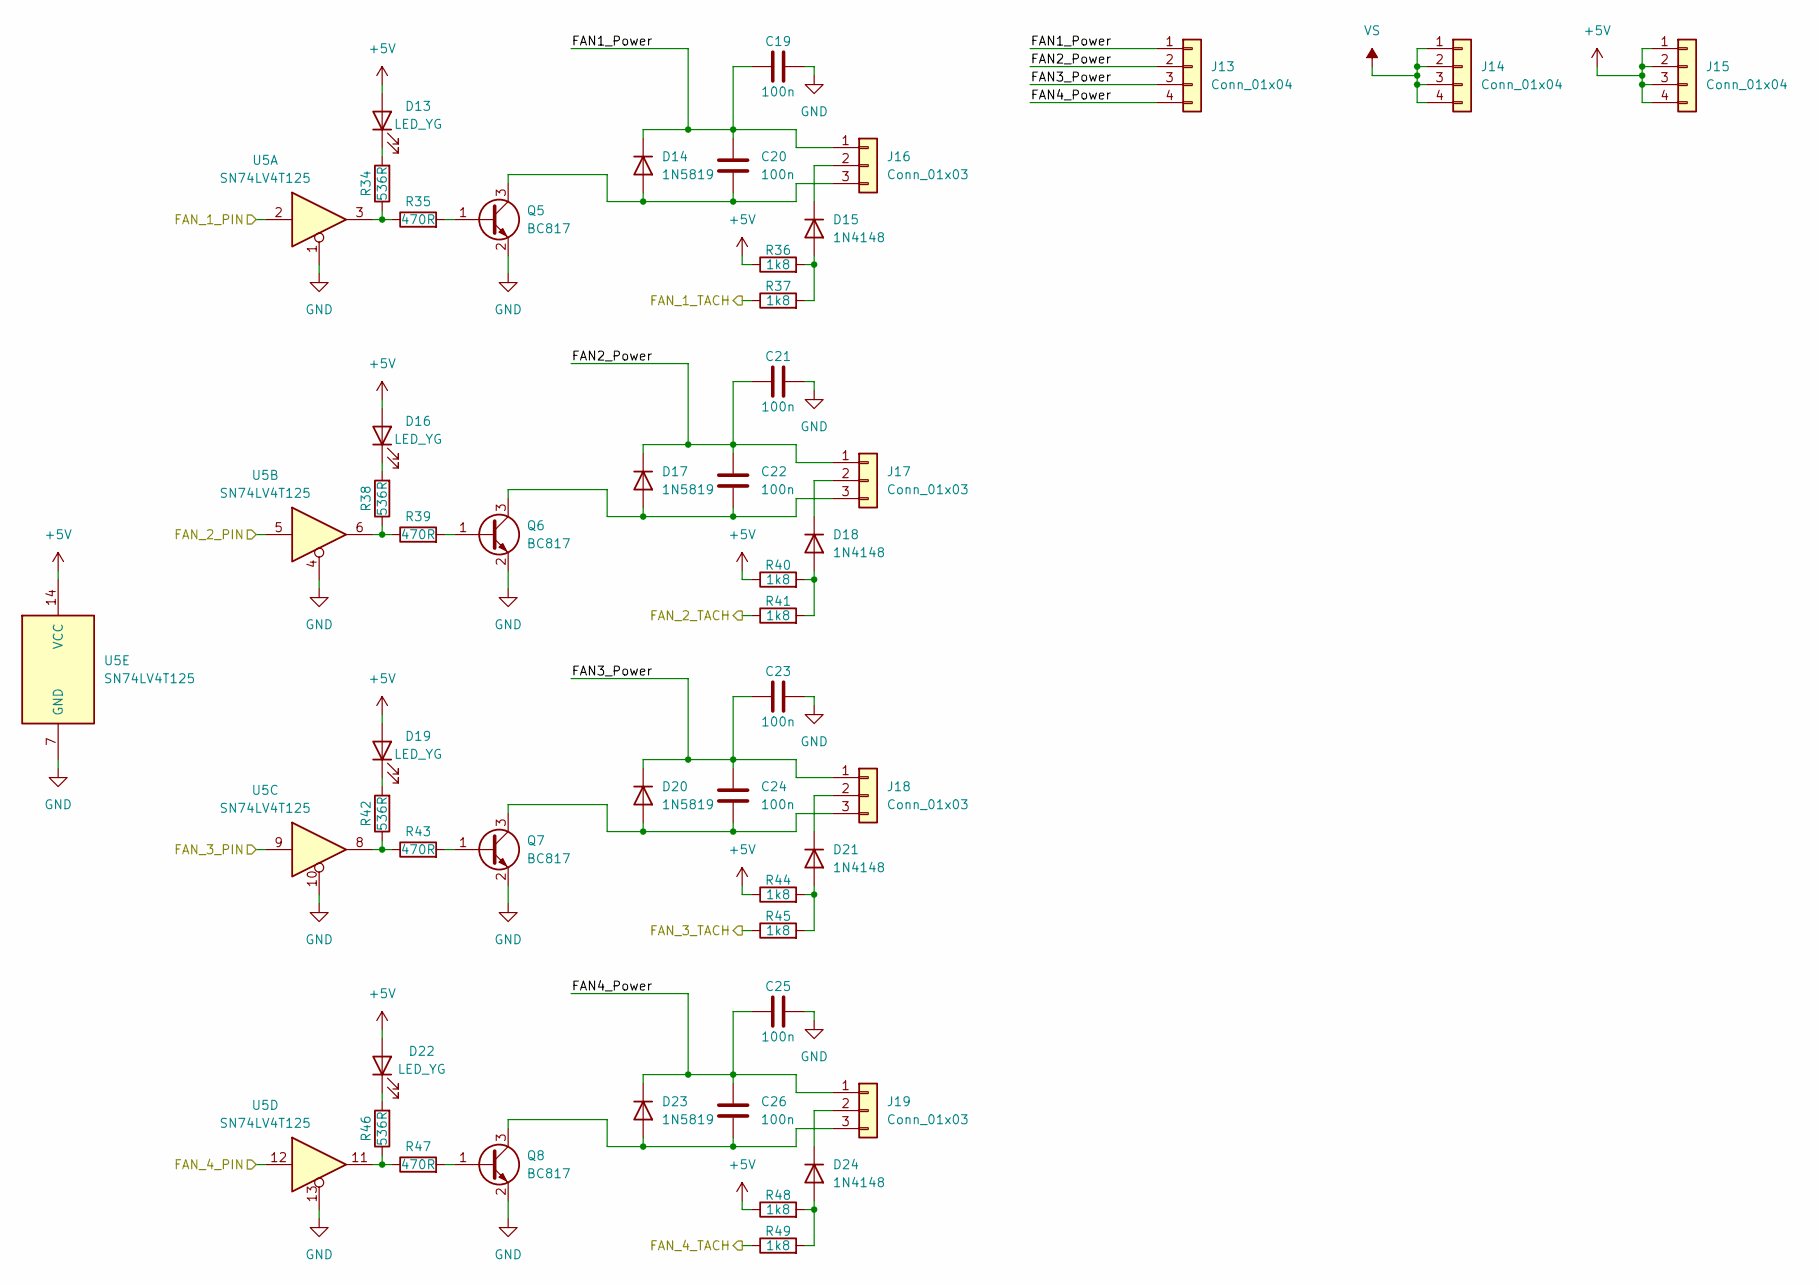
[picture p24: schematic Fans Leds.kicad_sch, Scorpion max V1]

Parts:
C19, C20, C21, C22, C23, C24, C25, C26: 100n; C_0603_1608Metric
D13, D16, D19, D22: LED_YG; LED_0603_1608Metric
D14, D17, D20, D23: 1N5819; D_SOD-323
D15, D18, D21, D24: 1N4148; D_SOD-523
J13, J14, J15: Conn_01x04; PinSocket_1x04_P2.54mm_Vertical
J16, J17, J18, J19: Conn_01x03; JST_XH_B3B-XH-A_1x03_P2.50mm_Vertical
Q5, Q6, Q7, Q8: BC817; SOT-23
R34, R38, R42, R46: 536R; R_0603_1608Metric
R35, R39, R43, R47: 470R; R_0603_1608Metric
R36, R37, R40, R41, R44, R45, R48, R49: 1k8; R_0603_1608Metric
U5: SN74LV4T125; TSSOP-14_4.4x5mm_P0.65mm

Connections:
+5V: D13.2 (A), D16.2 (A), D19.2 (A), D22.2 (A), J15.1, J15.2, J15.3, J15.4, R36.1, R40.1, R44.1, R48.1, U5.14 (VCC); also elsewhere on the board
/Fans Leds/FAN1_Power: C19.1, C20.1, D14.1 (K), J13.1, J16.1
/Fans Leds/FAN2_Power: C21.1, C22.1, D17.1 (K), J13.2, J17.1
/Fans Leds/FAN3_Power: C23.1, C24.1, D20.1 (K), J13.3, J18.1
/Fans Leds/FAN4_Power: C25.1, C26.1, D23.1 (K), J13.4, J19.1
/Fans Leds/FAN_1_PIN: U5.2; also elsewhere on the board
/Fans Leds/FAN_1_TACH: R37.1; also elsewhere on the board
/Fans Leds/FAN_2_PIN: U5.5; also elsewhere on the board
/Fans Leds/FAN_2_TACH: R41.1; also elsewhere on the board
/Fans Leds/FAN_3_PIN: U5.9; also elsewhere on the board
/Fans Leds/FAN_3_TACH: R45.1; also elsewhere on the board
/Fans Leds/FAN_4_PIN: U5.12; also elsewhere on the board
/Fans Leds/FAN_4_TACH: R49.1; also elsewhere on the board
GND: C19.2, C21.2, C23.2, C25.2, Q5.2 (E), Q6.2 (E), Q7.2 (E), Q8.2 (E), U5.1, U5.4, U5.7 (GND), U5.10, U5.13; also elsewhere on the board
unnamed: D13.1 (K), R34.2
unnamed: C20.2, D14.2 (A), J16.3, Q5.3 (C)
unnamed: D15.2 (A), R36.2, R37.2
unnamed: D15.1 (K), J16.2
unnamed: D16.1 (K), R38.2
unnamed: C22.2, D17.2 (A), J17.3, Q6.3 (C)
unnamed: D18.2 (A), R40.2, R41.2
unnamed: D18.1 (K), J17.2
unnamed: D19.1 (K), R42.2
unnamed: C24.2, D20.2 (A), J18.3, Q7.3 (C)
unnamed: D21.2 (A), R44.2, R45.2
unnamed: D21.1 (K), J18.2
unnamed: D22.1 (K), R46.2
unnamed: C26.2, D23.2 (A), J19.3, Q8.3 (C)
unnamed: D24.2 (A), R48.2, R49.2
unnamed: D24.1 (K), J19.2
unnamed: Q5.1 (B), R35.2
unnamed: Q6.1 (B), R39.2
unnamed: Q7.1 (B), R43.2
unnamed: Q8.1 (B), R47.2
unnamed: R34.1, R35.1, U5.3
unnamed: R38.1, R39.1, U5.6
unnamed: R42.1, R43.1, U5.8
unnamed: R46.1, R47.1, U5.11
VS: J14.1, J14.2, J14.3, J14.4; also elsewhere on the board

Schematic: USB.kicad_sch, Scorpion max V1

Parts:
C1: 100n; C_0603_1608Metric
C2: 4μ7; C_0805_2012Metric
D1: LED_R; LED_0603_1608Metric
D2: DSK24L; D_SOD-123F
J1: USB_A; USB-A-TH_USB-302-T
J2: USB_C_Receptacle_USB2.0_14P; USB-C_SMD-TYPE-C-31-M-12_1
R1: 47k; R_0603_1608Metric
R2: 620R; R_0603_1608Metric
R3, R4: 5k1; R_0603_1608Metric
S1: STMPS2141STR; SOT95P280X145-5N; Mouser Part Number 511-STMPS2141STR
U1: USBLC6-2SC6; SOT-23-6

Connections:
+5V: D2.1 (K), R1.1, R2.1, S1.5 (IN); also elsewhere on the board
/Microcontroller/PB12_GPIO: S1.4 (EN); also elsewhere on the board
/Microcontroller/PB13_GPIO: D1.1 (K), R1.2, S1.3 (FAULT); also elsewhere on the board
/USB/USB_A_D+: U1.1 (I/O1); also elsewhere on the board
/USB/USB_A_D-: U1.3 (I/O2); also elsewhere on the board
/USB/USB_A_VBUS: C1.1, C2.1, J1.1 (VBUS), S1.1 (OUT), U1.5 (VBUS)
/USB/USB_C_D+: J2.A6 (D+), J2.B6 (D+); also elsewhere on the board
/USB/USB_C_D-: J2.A7 (D-), J2.B7 (D-); also elsewhere on the board
GND: C1.2, C2.2, J1.4 (GND), J1.5 (Shield), J2.A1B12 (GND), J2.B1A12 (GND), J2.S1 (SHIELD), R3.2, R4.2, S1.2 (GND), U1.2 (GND); also elsewhere on the board
unnamed: D1.2 (A), R2.2
unnamed: D2.2 (A), J2.A4B9 (VBUS), J2.B4A9 (VBUS)
unnamed: J1.3 (D+), U1.6 (I/O1)
unnamed: J1.2 (D-), U1.4 (I/O2)
unnamed: J2.A5 (CC1), R3.1
unnamed: J2.B5 (CC2), R4.1

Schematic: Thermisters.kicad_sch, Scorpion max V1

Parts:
C93, C94, C95: 100n; C_0603_1608Metric
J32, J35, J38: Conn_01x03; PinSocket_1x03_P2.54mm_Vertical
J33, J36, J39: Conn_01x02; JST_XH_B2B-XH-A_1x02_P2.50mm_Vertical
J34, J37, J40: Conn_01x02; PinSocket_1x02_P2.54mm_Vertical

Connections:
+3.3V: J32.3, J35.3, J38.3; also elsewhere on the board
/Microcontroller/PB1_ADC1_INP5: C93.1, J32.2; also elsewhere on the board
/Microcontroller/PC0_ADC3_INP10: C95.1, J38.2; also elsewhere on the board
/Microcontroller/PC1_ADC2_INP11: C94.1, J35.2; also elsewhere on the board
GND: C93.2, C94.2, C95.2, J32.1, J35.1, J38.1; also elsewhere on the board
unnamed: J33.1, J34.1
unnamed: J33.2, J34.2
unnamed: J36.1, J37.1
unnamed: J36.2, J37.2
unnamed: J39.1, J40.1
unnamed: J39.2, J40.2

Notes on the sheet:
Thermister
Temp Module

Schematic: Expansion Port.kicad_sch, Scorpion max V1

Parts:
J11, J12: Conn_02x08_Odd_Even; PinSocket_2x08_P2.54mm_Vertical

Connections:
+3.3V: J11.14; also elsewhere on the board
+5V: J11.16, J12.16; also elsewhere on the board
/Expansion Port/GPIO_1: J12.1; also elsewhere on the board
/Expansion Port/GPIO_2: J12.2; also elsewhere on the board
/Expansion Port/GPIO_3: J12.3; also elsewhere on the board
/Expansion Port/GPIO_4: J12.4; also elsewhere on the board
/Expansion Port/GPIO_5: J12.5; also elsewhere on the board
/Expansion Port/GPIO_6: J12.6; also elsewhere on the board
/Expansion Port/GPIO_7: J12.7; also elsewhere on the board
/Expansion Port/GPIO_8: J12.8; also elsewhere on the board
/Expansion Port/GPIO_9: J12.9; also elsewhere on the board
/Expansion Port/GPIO_10: J12.10; also elsewhere on the board
/Expansion Port/GPIO_11: J12.11; also elsewhere on the board
/Expansion Port/GPIO_12: J12.12; also elsewhere on the board
/Expansion Port/RXD1: J11.6; also elsewhere on the board
/Expansion Port/RXD2: J11.10; also elsewhere on the board
/Expansion Port/SCL: J12.14; also elsewhere on the board
/Expansion Port/SDA: J12.13; also elsewhere on the board
/Expansion Port/SDIO_CK: J11.5; also elsewhere on the board
/Expansion Port/SDIO_CMD: J11.8; also elsewhere on the board
/Expansion Port/SDIO_D0: J11.1; also elsewhere on the board
/Expansion Port/SDIO_D1: J11.2; also elsewhere on the board
/Expansion Port/SDIO_D2: J11.3; also elsewhere on the board
/Expansion Port/SDIO_D3: J11.4; also elsewhere on the board
/Expansion Port/SPI_MISO: J11.12; also elsewhere on the board
/Expansion Port/SPI_MOSI: J11.13; also elsewhere on the board
/Expansion Port/SPI_SCK: J11.11; also elsewhere on the board
/Expansion Port/TXD1: J11.7; also elsewhere on the board
/Expansion Port/TXD2: J11.9; also elsewhere on the board
GND: J11.15, J12.15; also elsewhere on the board

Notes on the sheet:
Expansion Module

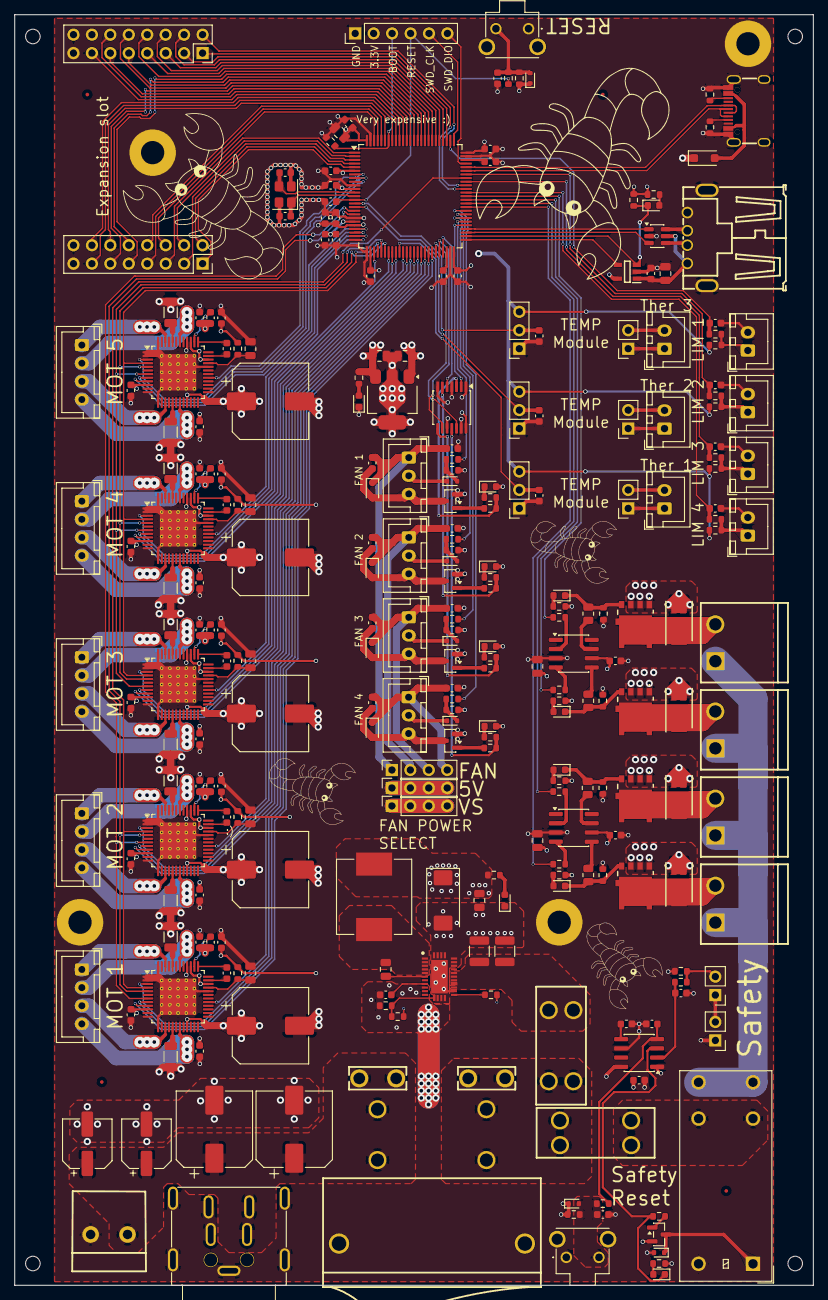
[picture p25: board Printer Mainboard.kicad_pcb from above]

Board: 4 copper layers, 110.0 x 175.0 mm, 279 parts (0 on the bottom side), 228 nets.

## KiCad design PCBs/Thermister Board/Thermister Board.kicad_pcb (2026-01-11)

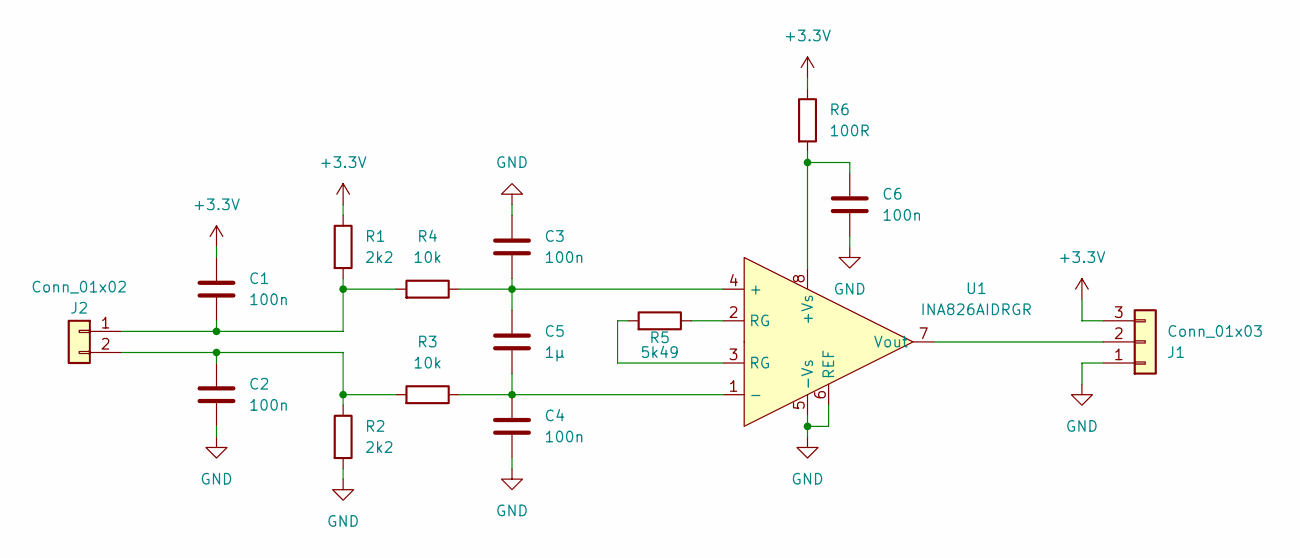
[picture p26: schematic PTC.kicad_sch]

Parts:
C1, C2, C3, C4, C6: 100n; C_0603_1608Metric
C5: 1µ; C_0603_1608Metric
J1: Conn_01x03; PinHeader_1x03_P2.54mm_Vertical
J2: Conn_01x02; PinHeader_1x02_P2.54mm_Vertical
R1, R2: 2k2; R_0603_1608Metric
R3, R4: 10k; R_0603_1608Metric
R5: 5k49; R_0603_1608Metric
R6: 100R; R_0603_1608Metric
U1: INA826AIDRGR; WSON-8-1EP_3x3mm_P0.5mm_EP1.45x2.4mm_ThermalVias

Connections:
+3.3V: C1.1, J1.3, R1.1, R6.1; also elsewhere on the board
GND: C2.2, C3.1, C4.2, C6.2, J1.1, R2.2, U1.5 (-Vs), U1.6 (REF); also elsewhere on the board
unnamed: C4.1, C5.2, R3.1, U1.1 (-), U1.9 (-)
unnamed: J1.2, U1.7 (Vout)
unnamed: C1.2, J2.1, R1.2, R4.2
unnamed: C2.1, J2.2, R2.1, R3.2
unnamed: R5.1, U1.2 (RG)
unnamed: R5.2, U1.3 (RG)
unnamed: C3.2, C5.1, R4.1, U1.4 (+)
unnamed: C6.1, R6.2, U1.8 (+Vs)

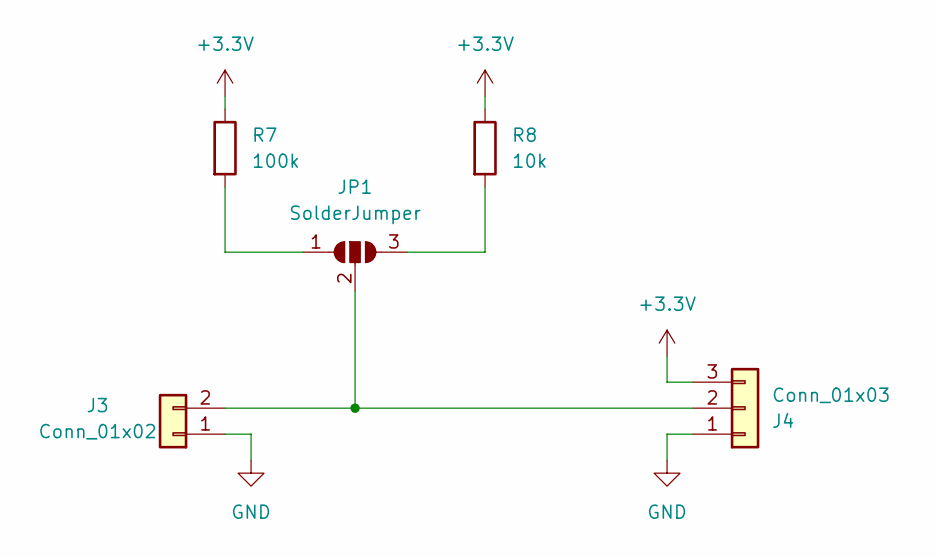
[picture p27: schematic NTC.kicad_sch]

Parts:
J3: Conn_01x02; PinHeader_1x02_P2.54mm_Vertical
J4: Conn_01x03; PinHeader_1x03_P2.54mm_Vertical
JP1: SolderJumper; SolderJumper-3_P1.3mm_Open_RoundedPad1.0x1.5mm_NumberLabels
R7: 100k; R_0603_1608Metric
R8: 10k; R_0603_1608Metric

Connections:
+3.3V: J4.3, R7.1, R8.1; also elsewhere on the board
GND: J3.1, J4.1; also elsewhere on the board
unnamed: J3.2, J4.2, JP1.2 (C)
unnamed: JP1.1 (A), R7.2
unnamed: JP1.3 (B), R8.2

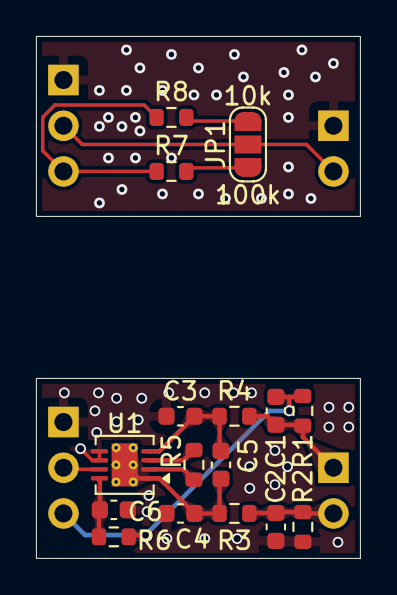
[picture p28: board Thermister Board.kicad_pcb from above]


Board: 2 copper layers, 18.0 x 29.0 mm, 20 parts (4 on the bottom side), 13 nets.

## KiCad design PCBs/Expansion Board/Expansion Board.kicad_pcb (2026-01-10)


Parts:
J1, J2: Conn_02x08_Odd_Even; PinHeader_2x08_P2.54mm_Vertical
J3, J4: Conn_02x05_Odd_Even; IDC-Header_2x05_P2.54mm_Vertical
R1, R2: 10k; R_0603_1608Metric

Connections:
+3.3V: J1.14, J4.8
+5V: J1.16, J2.16, J3.10, J4.10, R1.1, R2.1
/GPIO_1: J2.1
/GPIO_2: J2.2
/GPIO_3: J2.3
/GPIO_4: J2.4
/GPIO_5: J2.5
/GPIO_6: J2.6
/GPIO_7: J2.7, J4.3
/GPIO_8: J2.8, J4.4
/GPIO_9: J2.9, J4.7
/GPIO_10: J2.10, J4.5
/GPIO_11: J2.11, J3.7
/GPIO_12: J2.12, J3.8
/RXD1: J1.6, J3.2
/RXD2: J1.10, J3.3
/SCL: J2.14, J3.6, R1.2
/SDA: J2.13, J3.4, R2.2
/SDIO_CK: J1.5
/SDIO_CMD: J1.8
/SDIO_D0: J1.1
/SDIO_D1: J1.2
/SDIO_D2: J1.3
/SDIO_D3: J1.4
/SPI_MISO: J1.12, J4.1
/SPI_MOSI: J1.13, J4.6
/SPI_SCK: J1.11, J4.2
/TXD1: J1.7, J3.1
/TXD2: J1.9, J3.5
GND: J1.15, J2.15, J3.9, J4.9



Board: 2 copper layers, 24.0 x 37.0 mm, 6 parts (2 on the bottom side), 18 nets.

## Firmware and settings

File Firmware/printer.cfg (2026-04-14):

# This file is an example config file for cartesian style printers.
# One may copy and edit this file to configure a new cartesian
# printer.

# DO NOT COPY THIS FILE WITHOUT CAREFULLY READING AND UPDATING IT
# FIRST. Incorrectly configured parameters may cause damage.

# See docs/Config_Reference.md for a description of parameters.

[include mainsail.cfg]

[tmc2130 stepper_x]
cs_pin: PE12
spi_software_sclk_pin: PA9
spi_software_mosi_pin: PC3
spi_software_miso_pin: PC2
run_current: 0.5
#hold_current: 0.3
sense_resistor: 0.120
stealthchop_threshold: 999999

[stepper_x]
step_pin: PE13
dir_pin: PE14
enable_pin: !PE11
microsteps: 16
rotation_distance: 32
endstop_pin: ^!PA15
position_endstop: 0
position_max: 215
homing_speed: 50

[tmc2130 stepper_y]
cs_pin: PE8
spi_software_sclk_pin: PA9
spi_software_mosi_pin: PC3
spi_software_miso_pin: PC2
run_current: 0.8
#hold_current: 0.3
sense_resistor: 0.120
stealthchop_threshold: 999999

[stepper_y]
step_pin: PE9
dir_pin: PE10
enable_pin: !PE7
microsteps: 16
rotation_distance: 32
endstop_pin: ^!PA10
position_endstop: 0
position_max: 200
homing_speed: 50

[tmc2130 stepper_z]
cs_pin: PC5
spi_software_sclk_pin: PA5
spi_software_mosi_pin: PA7
spi_software_miso_pin: PA6
run_current: 0.5
hold_current: 0.2
sense_resistor: 0.120
stealthchop_threshold: 999999

[stepper_z]
step_pin: PB0
dir_pin: !PB2
enable_pin: !PC4
microsteps: 16
rotation_distance: 8
endstop_pin: ^!PA8
position_endstop: 0
#position_min: -0.5
position_max: 200

[tmc2130 stepper_z1]
cs_pin: PA2
spi_software_sclk_pin: PA5
spi_software_mosi_pin: PA7
spi_software_miso_pin: PA6
run_current: 0.5
hold_current: 0.2
sense_resistor: 0.120
stealthchop_threshold: 999999

[stepper_z1]
step_pin: PA3
dir_pin: !PA4
enable_pin: !PA1
microsteps: 16
rotation_distance: 8
#endstop_pin: ^!PA8

[tmc2130 extruder]
cs_pin: PC14
spi_software_sclk_pin: PA5
spi_software_mosi_pin: PA7
spi_software_miso_pin: PA6
run_current: 0.8
#hold_current: 0.25
sense_resistor: 0.120
stealthchop_threshold: 999999

[extruder]
step_pin: PC15
dir_pin: PA0
enable_pin: !PC13
microsteps: 128
rotation_distance: 33.684
nozzle_diameter: 0.400
filament_diameter: 1.750
heater_pin: PC6
#max_power: 0.5
sensor_type: Generic 3950
pullup_resistor: 4700
sensor_pin: PC0
control: pid
pid_Kp: 22.2
pid_Ki: 1.08
pid_Kd: 114
min_temp: 0
max_temp: 250

[heater_bed]
heater_pin: PD15
#max_power: 0.5
#pwm_cycle_time: 0.100
sensor_type: Generic 3950
pullup_resistor: 4700
sensor_pin: PC1
control: watermark
min_temp: 0
max_temp: 300

[fan]
pin: PD8

[heater_fan heatbreak_cooling_fan]
pin: PB11

[mcu]
serial: /dev/serial/by-id/usb-Klipper_stm32h743xx_1B0046001951333337383632-if00
baud: 250000
restart_method: command

[printer]
kinematics: cartesian
max_velocity: 400
max_accel: 1500
max_z_velocity: 15
max_z_accel: 30

[gcode_arcs]
resolution: 0.25



## TMC2130 config
#[tmc2130 stepper_x]
#cs_pin:
#   The pin corresponding to the TMC2130 chip select line. This pin
#   will be set to low at the start of SPI messages and raised to high
#   after the message completes. This parameter must be provided.
#spi_speed:
#spi_bus:
#spi_software_sclk_pin:
#spi_software_mosi_pin:
#spi_software_miso_pin:
#   See the "common SPI settings" section for a description of the
#   above parameters.
#chain_position:
#chain_length:
#   These parameters configure an SPI daisy chain. The two parameters
#   define the stepper position in the chain and the total chain length.
#   Position 1 corresponds to the stepper that connects to the MOSI signal.
#   The default is to not use an SPI daisy chain.
#interpolate: True
#   If true, enable step interpolation (the driver will internally
#   step at a rate of 256 micro-steps). This interpolation does
#   introduce a small systemic positional deviation - see
#   TMC_Drivers.md for details. The default is True.
#run_current:
#   The amount of current (in amps RMS) to configure the driver to use
#   during stepper movement. This parameter must be provided.
#hold_current:
#   The amount of current (in amps RMS) to configure the driver to use
#   when the stepper is not moving. Setting a hold_current is not
#   recommended (see TMC_Drivers.md for details). The default is to
#   not reduce the current.
#sense_resistor: 0.110
#   The resistance (in ohms) of the motor sense resistor. The default
#   is 0.110 ohms.
#stealthchop_threshold: 0
#   The velocity (in mm/s) to set the "stealthChop" threshold to. When
#   set, "stealthChop" mode will be enabled if the stepper motor
#   velocity is below this value. Note that the "sensorless homing"
#   code may temporarily override this setting during homing
#   operations. The default is 0, which disables "stealthChop" mode.
#coolstep_threshold:
#   The velocity (in mm/s) to set the TMC driver internal "CoolStep"
#   threshold to. If set, the coolstep feature will be enabled when
#   the stepper motor velocity is near or above this value. Important
#   - if coolstep_threshold is set and "sensorless homing" is used,
#   then one must ensure that the homing speed is above the coolstep
#   threshold! The default is to not enable the coolstep feature.
#high_velocity_threshold:
#   The velocity (in mm/s) to set the TMC driver internal "high
#   velocity" threshold (THIGH) to. This is typically used to disable
#   the "CoolStep" feature at high speeds. The default is to not set a
#   TMC "high velocity" threshold.
#driver_MSLUT0: 2863314260
#driver_MSLUT1: 1251300522
#driver_MSLUT2: 608774441
#driver_MSLUT3: 269500962
#driver_MSLUT4: 4227858431
#driver_MSLUT5: 3048961917
#driver_MSLUT6: 1227445590
#driver_MSLUT7: 4211234
#driver_W0: 2
#driver_W1: 1
#driver_W2: 1
#driver_W3: 1
#driver_X1: 128
#driver_X2: 255
#driver_X3: 255
#driver_START_SIN: 0
#driver_START_SIN90: 247
#   These fields control the Microstep Table registers directly. The optimal
#   wave table is specific to each motor and might vary with current. An
#   optimal configuration will have minimal print artifacts caused by
#   non-linear stepper movement. The values specified above are the default
#   values used by the driver. The value must be specified as a decimal integer
#   (hex form is not supported). In order to compute the wave table fields,
#   see the tmc2130 "Calculation Sheet" from the Trinamic website.
#driver_IHOLDDELAY: 8
#driver_TPOWERDOWN: 0
#driver_TBL: 1
#driver_TOFF: 4
#driver_HEND: 7
#driver_HSTRT: 0
#driver_VHIGHFS: 0
#driver_VHIGHCHM: 0
#driver_PWM_AUTOSCALE: True
#driver_PWM_FREQ: 1
#driver_PWM_GRAD: 4
#driver_PWM_AMPL: 128
#driver_FREEWHEEL: 0
#driver_SGT: 0
#driver_SEMIN: 0
#driver_SEUP: 0
#driver_SEMAX: 0
#driver_SEDN: 0
#driver_SEIMIN: 0
#driver_SFILT: 0
#   Set the given register during the configuration of the TMC2130
#   chip. This may be used to set custom motor parameters. The
#   defaults for each parameter are next to the parameter name in the
#   above list.
#diag0_pin:
#diag1_pin:
#   The micro-controller pin attached to one of the DIAG lines of the
#   TMC2130 chip. Only a single diag pin should be specified. The pin
#   is "active low" and is thus normally prefaced with "^!". Setting
#   this creates a "tmc2130_stepper_x:virtual_endstop" virtual pin
#   which may be used as the stepper's endstop_pin. Doing this enables
#   "sensorless homing". (Be sure to also set driver_SGT to an
#   appropriate sensitivity value.) The default is to not enable
#   sensorless homing.


[display]
lcd_type: ssd1306
#   Set to either "ssd1306" or "sh1106" for the given display type.
#i2c_mcu:
#i2c_bus:
i2c_software_scl_pin: PB6
i2c_software_sda_pin: PB7
#i2c_speed:
#   Optional parameters available for displays connected via an i2c
#   bus. See the "common I2C settings" section for a description of
#   the above parameters.
#cs_pin:
#dc_pin:
#spi_speed:
#spi_bus:
#spi_software_sclk_pin:
#spi_software_mosi_pin:
#spi_software_miso_pin:
#   The pins connected to the lcd when in "4-wire" spi mode. See the
#   "common SPI settings" section for a description of the parameters
#   that start with "spi_". The default is to use i2c mode for the
#   display.
reset_pin: PD7
#   A reset pin may be specified on the display. If it is not
#   specified then the hardware must have a pull-up on the
#   corresponding lcd line.
#contrast:
#   The contrast to set. The value may range from 0 to 256 and the
#   default is 239.
#vcomh: 0
#   Set the Vcomh value on the display. This value is associated with
#   a "smearing" effect on some OLED displays. The value may range
#   from 0 to 63. Default is 0.
#invert: False
#   TRUE inverts the pixels on certain OLED displays.  The default is
#   False.
#x_offset: 0
#   Set the horizontal offset value on SH1106 displays. The default is
#   0.

encoder_pins: ^PD4, ^PE0
click_pin: ^!PD0

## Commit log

2026-01-10 git is so hard to use
    [BOM_LCSC.xlsx, DC_DC Converter.kicad_sch, Expansion Board.csv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]
2026-01-11 Updated KiCad files and made 3D files for expansion board and thermister board
    [Printer Mainboard.kicad_sch, Thermister Board.kicad_pcb, bom.csv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]
2026-01-11 Updated all the files so its up to date
    [BOM_LCSC.xlsx, bom.csv, designators.csv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]
2026-01-11 Added Firmware for Marlin
    [corexy-boilerplate.cfg]
2026-01-11 Update README with schematic, PCB, and BOM information
    Added sections for schematic, PCB, and BOM details.
2026-01-11 Add images for PCB and related boards in README
2026-01-11 Added schematics in pdf format for the boards and interactive BOMs
    [BOM_LCSC.xlsx]
2026-01-11 Added pictures of prices in the BOM
    [BOM_LCSC.xlsx]
2026-01-11 Revise README for mainboard features and specifications
    Updated the README to improve clarity and detail about the main board's capabilities, including its specifications and intended use.
2026-01-11 Revise README section titles and add design overview
    Updated section titles and added a description of the board's design features.
2026-01-11 Enhance design description in README
    Expanded the design section to include details about PCB trace width and layout.
2026-01-12 Made final changes before submiting
    [BOM_FROM_LCSC.xls, BOM_GLOBAL.xlsx, BOM_LCSC.xlsx]
2026-01-14 Added .csv BOMs
    added .csv files
    [BOM_FROM_LCSC.csv, BOM_GLOBAL.csv]
2026-01-14 Include schematic images in README
    Added images of schematics for various boards to README.
2026-03-26 Fixed some PCB stuff and rendering
    [Expansion Board.kicad_sch, Printer Mainboard.kicad_pcb, SCORPION MAX V1 Video.blend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]
2026-04-14 Added new clipper software cfg file
    [corexy-boilerplate.cfg, printer.cfg]
2026-04-14 Fixed .history track stuff
2026-04-15 Add video demonstration section to README
    Added a video link showcasing the functionality of the board.
2026-04-15 Added picture of the board
